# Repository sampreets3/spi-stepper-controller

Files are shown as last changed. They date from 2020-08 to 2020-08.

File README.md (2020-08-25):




# spi-stepper-controller
Design for an SPI based bipolar stepper motor controller, useful in robotic/3D printing applications. Makes use of the MCP23S08 SPI based I/O expander. Ideal for applications where number of GPIO is constrained. Provided with accompanying library to interface with the board.

<p align="center">
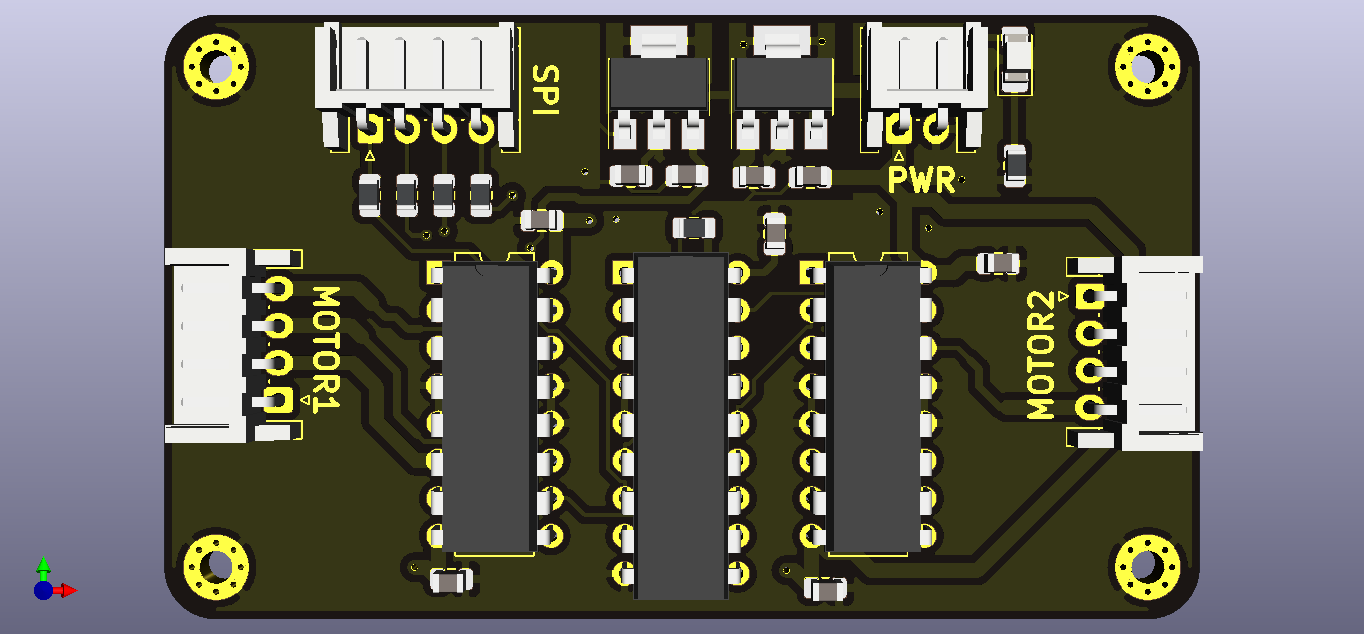
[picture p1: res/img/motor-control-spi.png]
rendered-pcb
  
</p>

---

## Considerations

- The design uses L293D dual H-bridge motor drivers, hence the peak current is maxed out at 1.5 A. Will not be able to drive larger stepper motors which have a higher current requirement.
- Maximum input voltage for the AMS1117-5.0 LDO chip is 15V. For best results, use ~12V supply.
- If you are working with unipolar stepper motors, change the MOTOR1 and MOTOR2 connectors to 5 pin and leave the common terminal unconnected.

---

## Schematic and Renderings

### Schematic
<details>
  <summary>Click to view the full schematic</summary>

<p align="center">
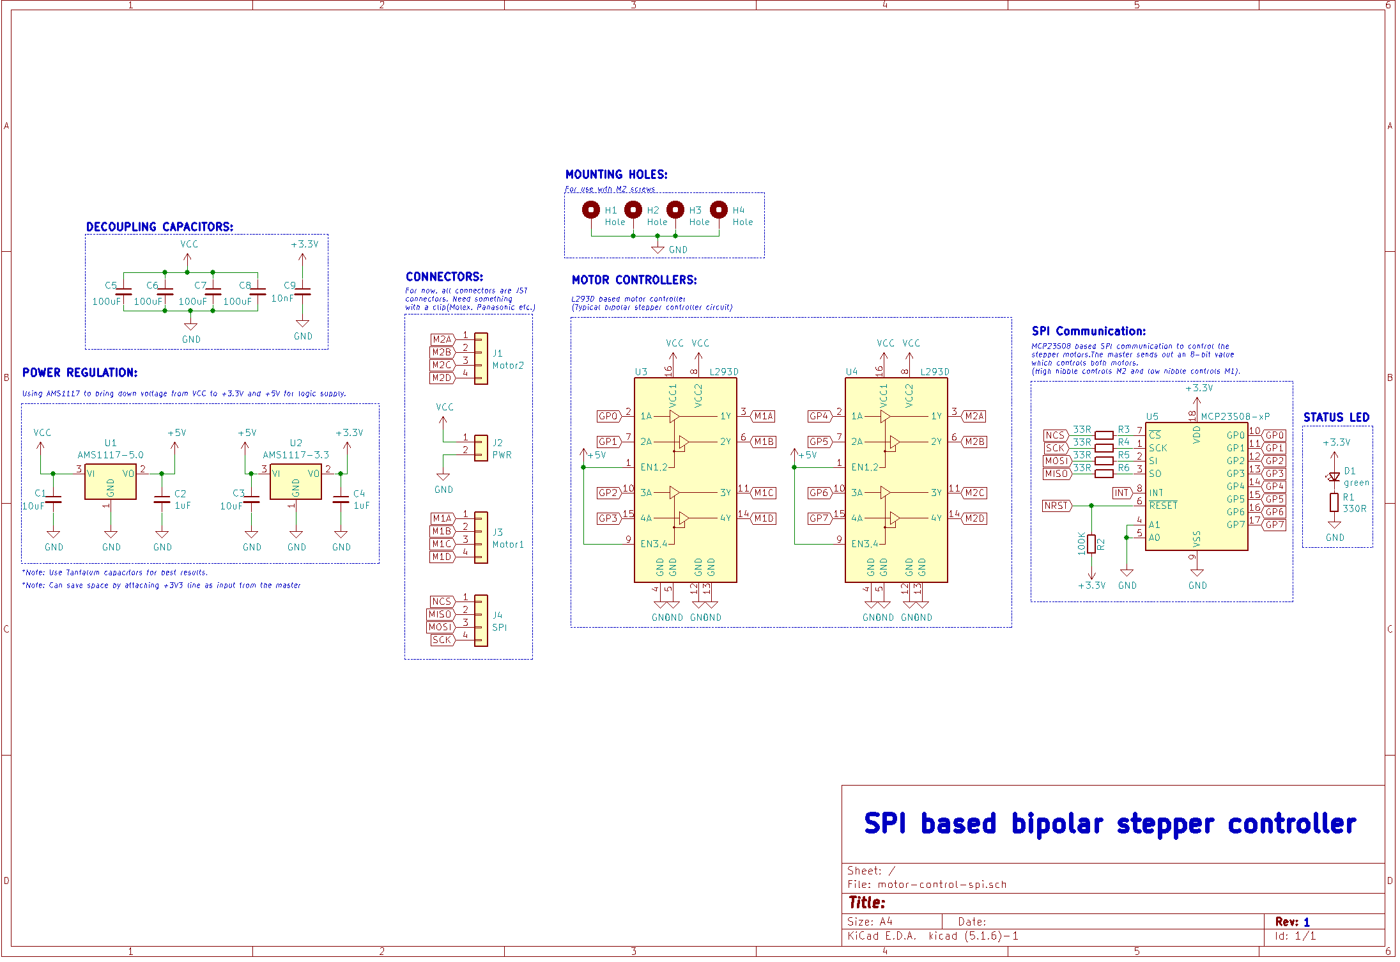
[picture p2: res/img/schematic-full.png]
schematics-full
  
</p>

</details>

### Layout
<details>
  <summary>Click to view the board layout</summary>
<!--
<p align="center">
  <img src="your_relative_path_here" width="350" title="schematics-full">
</p>
-->
</details>

---

## Contribute

- Clone or fork this repo : `git clone https://github.com/sampreets3/spi-stepper-controller.git`
- Make changes to your design and create a PR for merging

---

## Contact

You can reach me at `sampreets3@gmail.com`

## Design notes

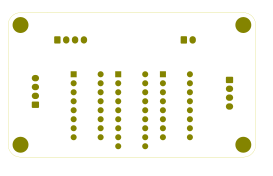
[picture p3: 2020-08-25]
res/img/motor-control-spi-B_Mask.png

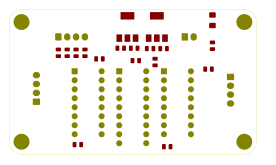
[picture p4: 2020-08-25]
res/img/motor-control-spi-F_Mask.png

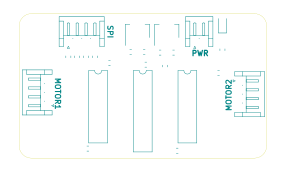
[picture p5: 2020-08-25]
res/img/motor-control-spi-F_SilkS.png

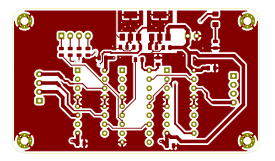
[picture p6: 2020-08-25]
res/img/motor-control-spi-F_Cu.png

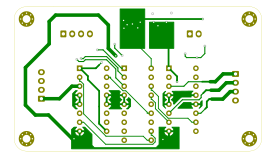
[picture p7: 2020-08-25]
res/img/motor-control-spi-B_Cu.png

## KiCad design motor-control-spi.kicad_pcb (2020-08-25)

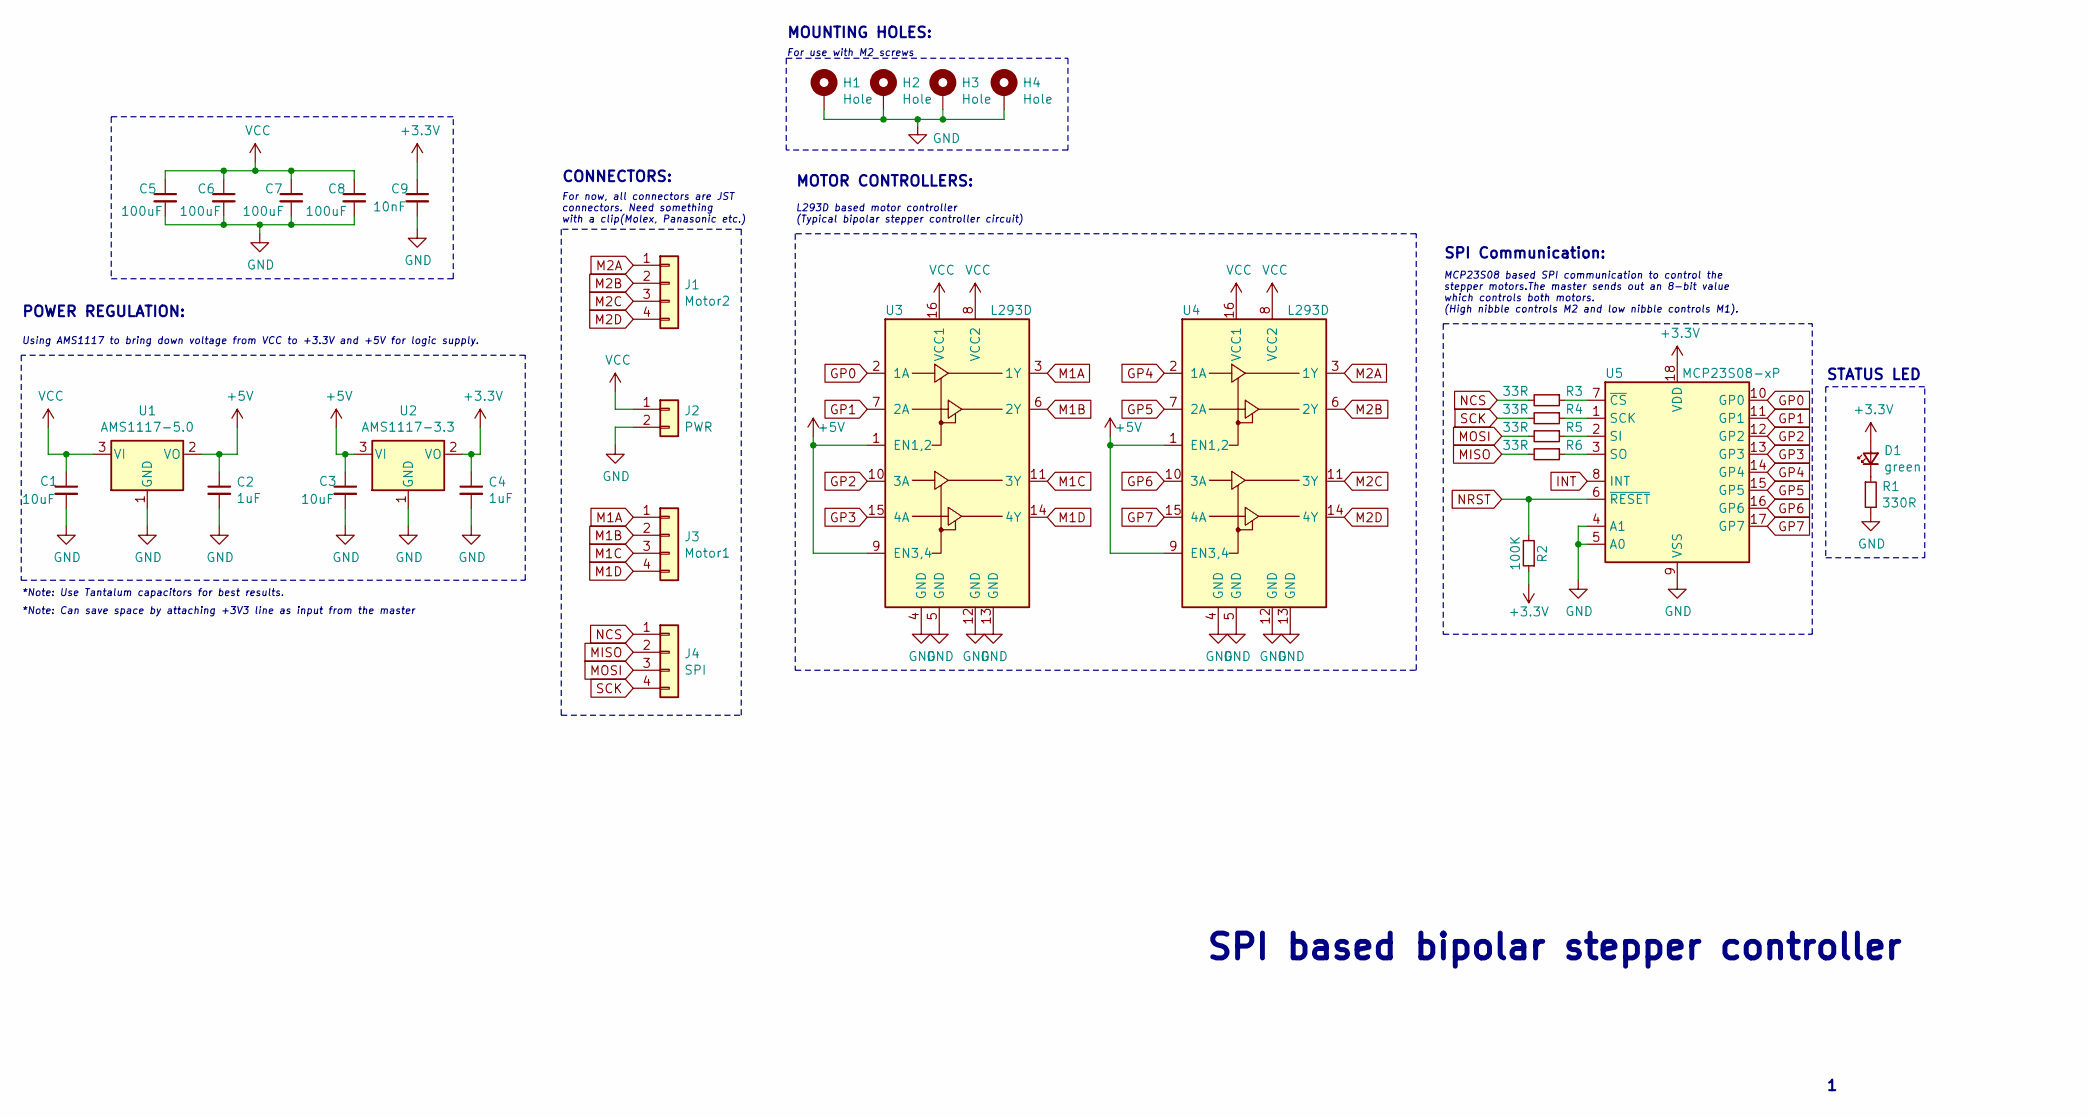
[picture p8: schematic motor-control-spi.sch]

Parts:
C1, C3: 10uF; C_0805_2012Metric
C2, C4: 1uF; C_0805_2012Metric
C5, C6, C7, C8: 100uF; C_0805_2012Metric
C9: 10nF; C_0805_2012Metric
D1: green; LED_1206_3216Metric_Pad1.42x1.75mm_HandSolder
H1, H2, H3, H4: Hole; MountingHole_2.2mm_M2_Pad_Via
J1: Motor2; JST_EH_S4B-EH_1x04_P2.50mm_Horizontal
J2: PWR; JST_EH_S2B-EH_1x02_P2.50mm_Horizontal
J3: Motor1; JST_EH_S4B-EH_1x04_P2.50mm_Horizontal
J4: SPI; JST_EH_S4B-EH_1x04_P2.50mm_Horizontal
R1: 330R; R_0805_2012Metric
R2: 100K; R_0805_2012Metric
R3, R4, R5, R6: 33R; R_0805_2012Metric
U1: AMS1117-5.0; SOT-223-3_TabPin2
U2: AMS1117-3.3; SOT-223-3_TabPin2
U3, U4: L293D; DIP-16_W7.62mm
U5: MCP23S08-xP; DIP-18_W7.62mm

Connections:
+3V3: C4.1, C9.1, D1.2 (A), R2.1, U2.2 (VO), U5.18 (VDD)
+5V: C2.1, C3.1, U1.2 (VO), U2.3 (VI), U3.1 (EN1,2), U3.9 (EN3,4), U4.1 (EN1,2), U4.9 (EN3,4)
GND: C1.2, C2.2, C3.2, C4.2, C5.2, C6.2, C7.2, C8.2, C9.2, H1.1, H2.1, H3.1, H4.1, J2.2, R1.2, U1.1 (GND), U2.1 (GND), U3.4 (GND), U3.5 (GND), U3.12 (GND), U3.13 (GND), U4.4 (GND), U4.5 (GND), U4.12 (GND), U4.13 (GND), U5.4 (A1), U5.5 (A0), U5.9 (VSS)
GP0: U3.2 (1A), U5.10 (GP0)
GP1: U3.7 (2A), U5.11 (GP1)
GP2: U3.10 (3A), U5.12 (GP2)
GP3: U3.15 (4A), U5.13 (GP3)
GP4: U4.2 (1A), U5.14 (GP4)
GP5: U4.7 (2A), U5.15 (GP5)
GP6: U4.10 (3A), U5.16 (GP6)
GP7: U4.15 (4A), U5.17 (GP7)
INT: U5.8 (INT)
M1A: J3.1, U3.3 (1Y)
M1B: J3.2, U3.6 (2Y)
M1C: J3.3, U3.11 (3Y)
M1D: J3.4, U3.14 (4Y)
M2A: J1.1, U4.3 (1Y)
M2B: J1.2, U4.6 (2Y)
M2C: J1.3, U4.11 (3Y)
M2D: J1.4, U4.14 (4Y)
MISO: J4.2, R6.2
MOSI: J4.3, R5.2
NCS: J4.1, R3.2
NRST: R2.2, U5.6 (~RESET)
unnamed: D1.1 (K), R1.1
unnamed: R3.1, U5.7 (~CS)
unnamed: R4.1, U5.1 (SCK)
unnamed: R5.1, U5.2 (SI)
unnamed: R6.1, U5.3 (SO)
SCK: J4.4, R4.2
VCC: C1.1, C5.1, C6.1, C7.1, C8.1, J2.1, U1.3 (VI), U3.8 (VCC2), U3.16 (VCC1), U4.8 (VCC2), U4.16 (VCC1)

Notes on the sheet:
MOUNTING HOLES:
For use with M2 screws
POWER REGULATION:
Using AMS1117 to bring down voltage from VCC to +3.3V and +5V for logic supply.
*Note: Use Tantalum capacitors for best results.
*Note: Can save space by attaching +3V3 line as input from the master
CONNECTORS:
For now, all connectors are JST connectors. Need something with a clip(Molex, Panasonic etc.)
MOTOR CONTROLLERS:
L293D based motor controller (Typical bipolar stepper controller circuit)
SPI Communication:
MCP23S08 based SPI communication to control the stepper motors.The master sends out an 8-bit value which controls both motors. (High nibble controls M2 and low nibble controls M1).
STATUS LED
SPI based bipolar stepper controller

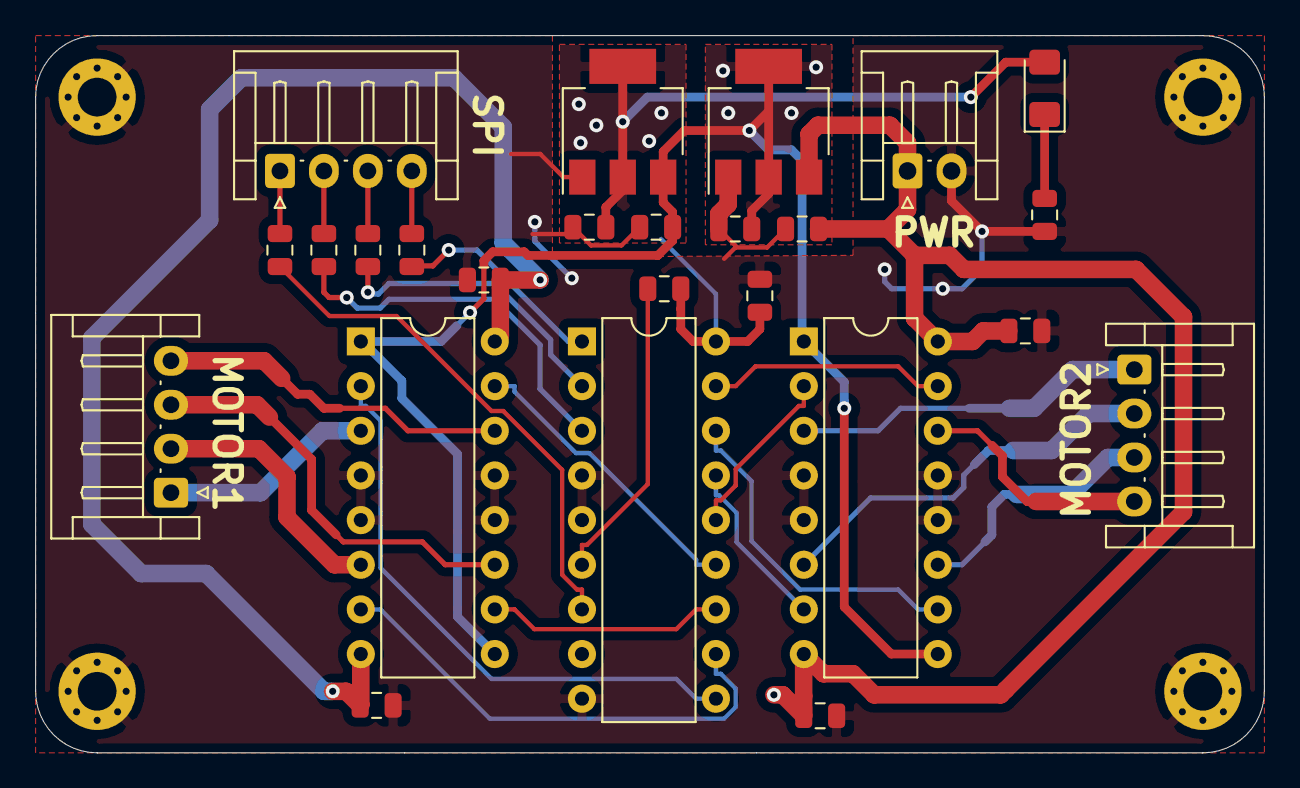
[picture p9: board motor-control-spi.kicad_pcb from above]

Board: 2 copper layers, 69.9 x 40.8 mm, 29 parts (0 on the bottom side), 30 nets.

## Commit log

2020-08-25 Added support libraries
    [motor-control-spi.sch]
2020-08-25 Added images and schematics to README

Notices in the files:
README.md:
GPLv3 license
